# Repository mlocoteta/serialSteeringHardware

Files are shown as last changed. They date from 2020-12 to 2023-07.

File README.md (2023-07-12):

# LKAS/ECU Data Interceptor

This is open source hardware for use with 2016/2017 Honda Accord's with Nidec camera units. Other form factors aren't guaranteed to fit - use at your own risk!

Link which demonstrates functionality:
<https://youtu.be/dwGLrD5iYao>
# Boards
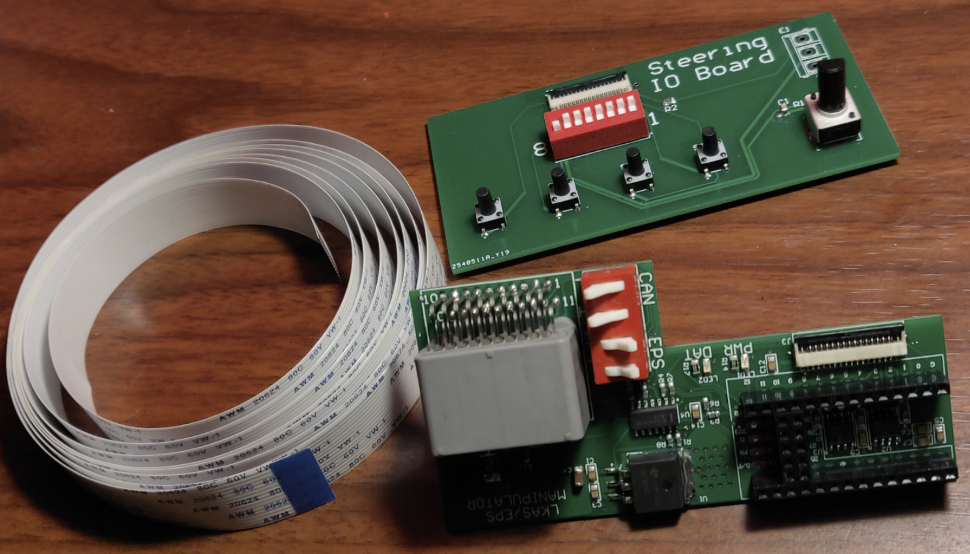
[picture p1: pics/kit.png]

There are two boards in this package:
1. The LKAS/ECU Manipulator
2. The debug board

To connect the debug board to the LKAS/ECU Manipulator a 15 position 0.1" ribbon cable should be used. This is needed for debugging and testing different scenarios.

## LKAS/ECU Manipulator V2

[Click here to purchase Development board.](https://devinstruments.com/)

Smaller form factor using STM32F1 MCU.

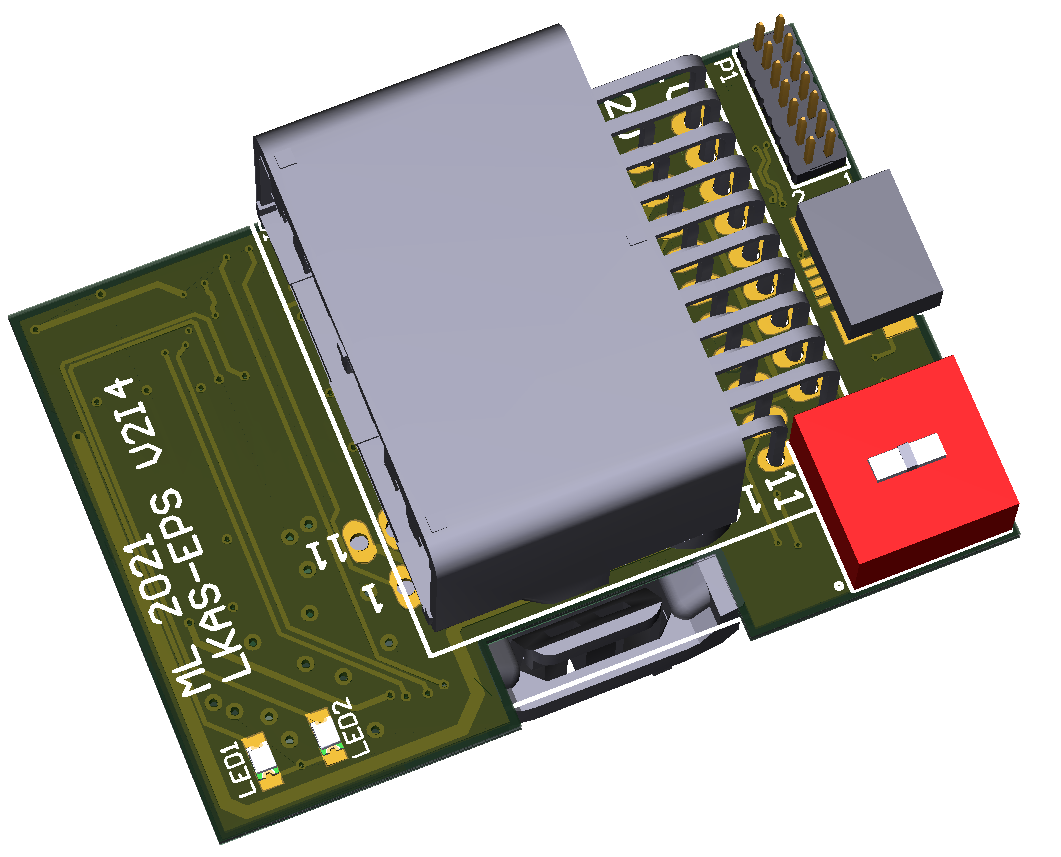
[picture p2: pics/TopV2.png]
LKAS/ECU Manipulator Version 2 (TOP)

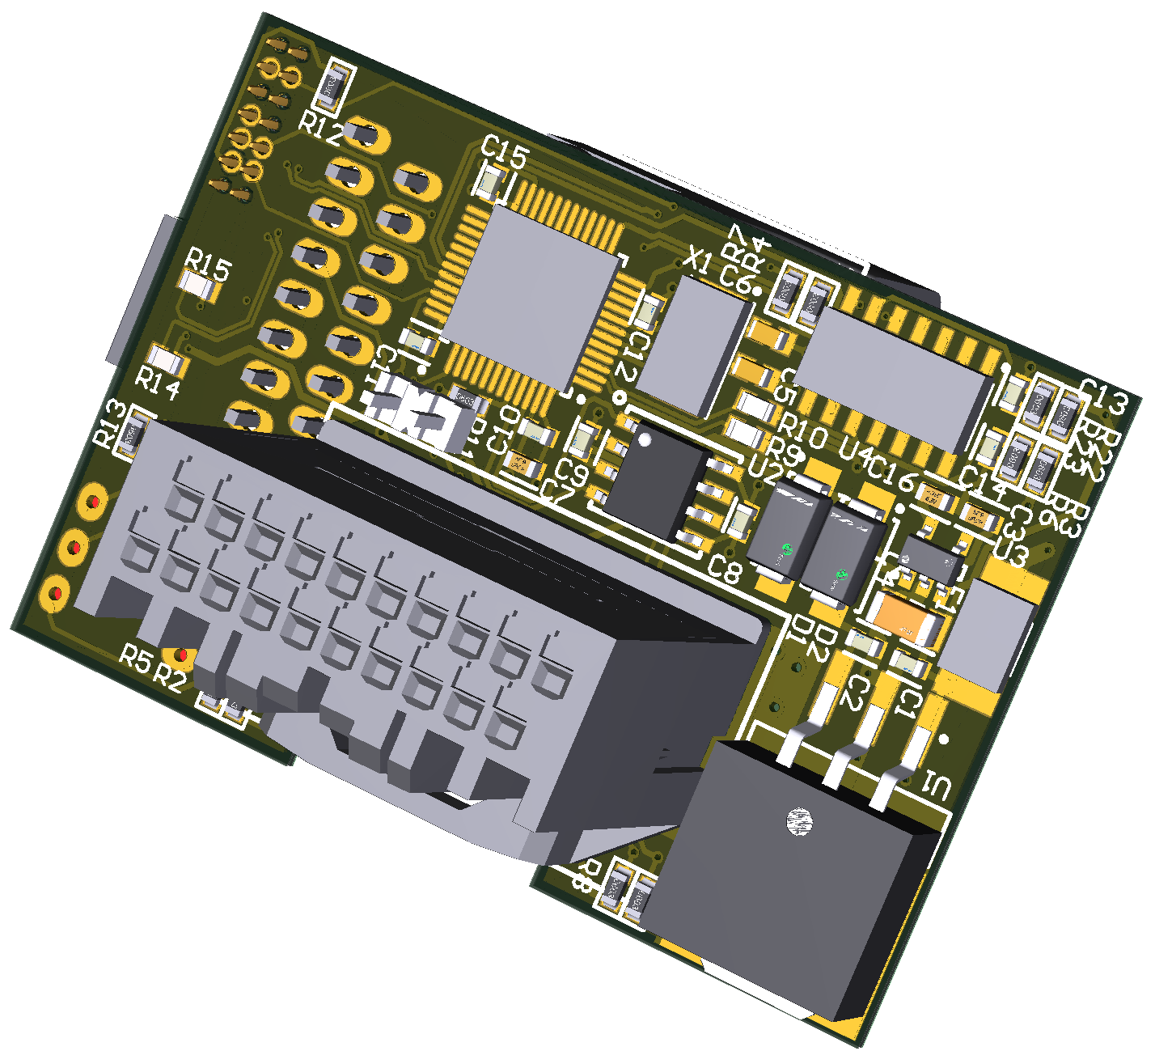
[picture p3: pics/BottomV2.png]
LKAS/ECU Manipulator Version 2 (Bottom)


## LKAS/ECU Manipulator V1

Below is the basic layout and functions of the board. 
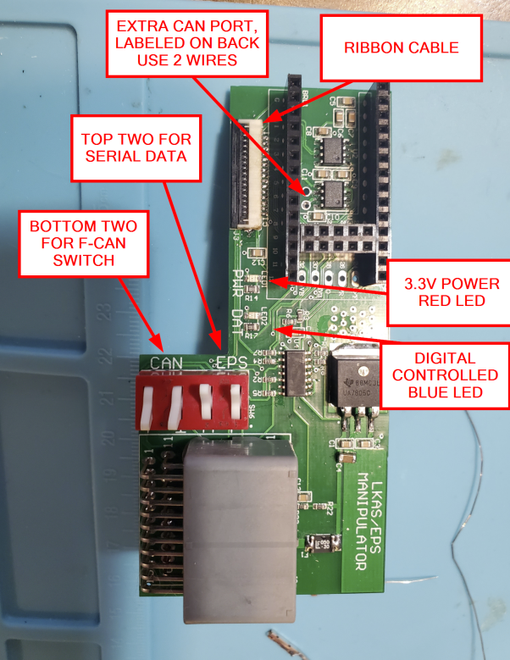
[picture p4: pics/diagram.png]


The board consists of: 
- A comparator for-
	- Level shifting the 12V to 3.3V to read serial information.
	- Level shifting the 3.3V UART to 12V to transmit on the vehicles serial line.
- Two MCP2562FDs for-
	- Transmitting/ receiving F-CAN from the vehicle
	- Transmitting/ receiving F-CAN to the camera unit.
		- **Note**: Typically this is not used.
- Debug Connector with GPIO and an ADC input
- Teensy 4.0 

When mounted the board is slightly larger than the the factory cover can contain. 
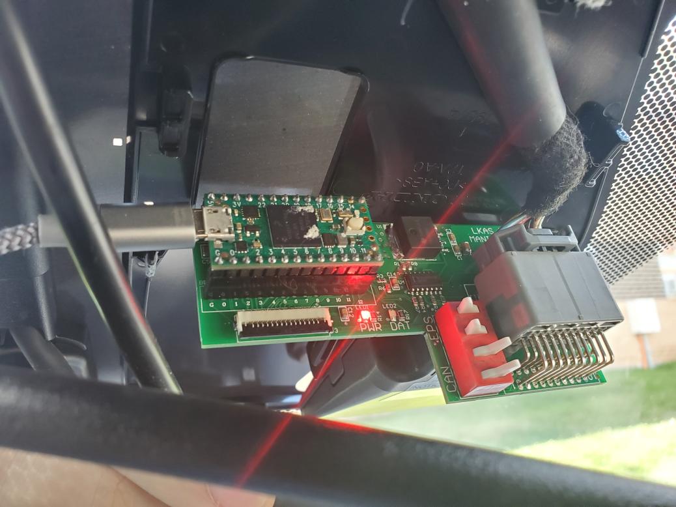
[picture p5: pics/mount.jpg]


## Debug Board
The board consists of: 
- A connection for a potentiometer **OR** a 3 block terminal for external resistance.
	- **Note**: This is current limited resulting in slightly lower/higher ADC readout values.
- 4 Tactile Push Buttons 
- 8 Position DIP Switch
	- *DIP 1-7* are digital IO
	- *DIP 8* to onboard POT/ External Pot
- Ribbon cable connector
## Firmware
For the latest OP open source firmware - visit:
V1 Board:
[https://github.com/reddn/AccordManualSteering](https://github.com/reddn/AccordManualSteering)

V2 Board:
[https://github.com/reddn/LINInterfaceV2](https://github.com/reddn/LINInterfaceV2)
In the Firmware Folder is an example sketch which simulates can simulate a brief torque to the steering wheel.

## License and Terms of Use:

Released under the MIT license.

**THIS IS ALPHA QUALITY HARDWARE AND IS INTENDED FOR OFF-ROAD USE AND RESEARCH PURPOSES ONLY.
YOU ARE RESPONSIBLE FOR COMPLYING WITH LOCAL LAWS AND REGULATIONS.
NO WARRANTY EXPRESSED OR IMPLIED.**

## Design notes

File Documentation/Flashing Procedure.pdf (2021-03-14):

Flashing Procedure | 03/14/2021

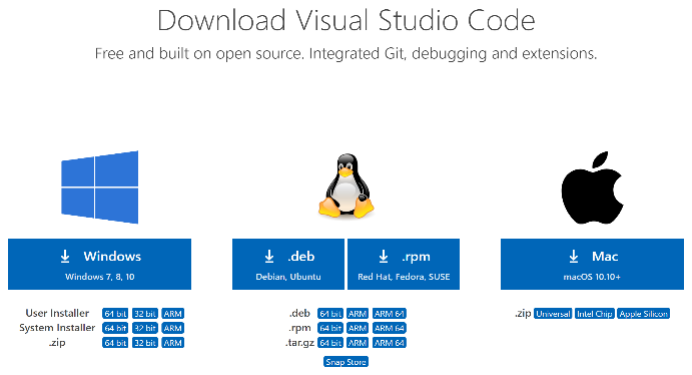
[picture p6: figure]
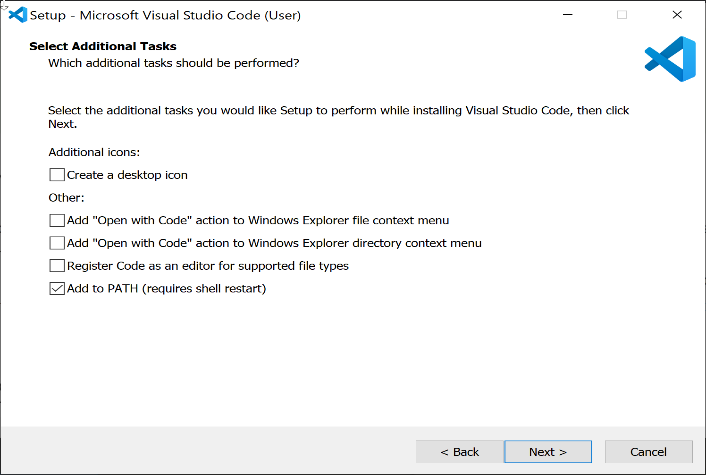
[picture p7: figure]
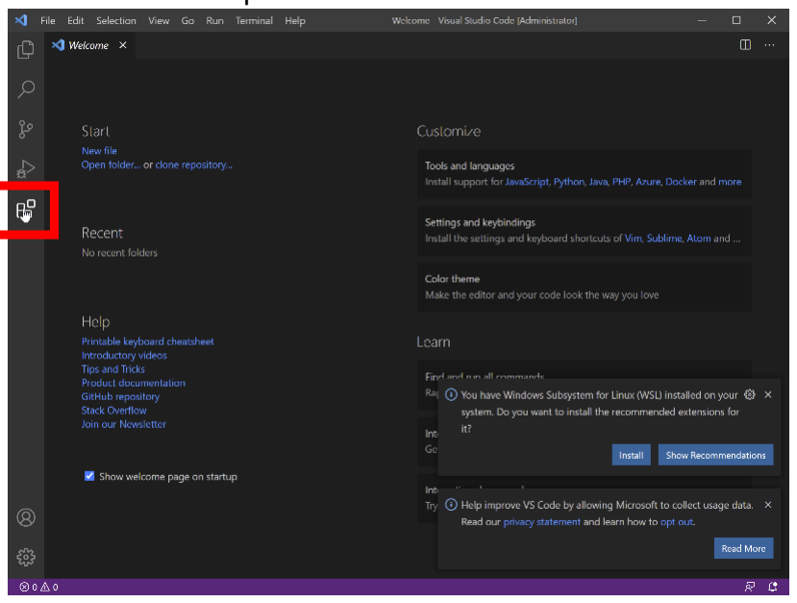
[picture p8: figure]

Doc Rev: A | Page 1 of 6

The EPS-LKAS V2 board is equipped with a Micro-B USB for flashing. The scope of this document is to get your computer setup with the necessary software to update and modify the firmware on your (Windows) computer.

1. Download and install Visual Studio Code. https://code.visualstudio.com/download
a. Download the program selecting the appropriate OS. Windows 10 will be used as an example for this document.
b. The default options should be fine for normal use, however, check options as needed.
c. Launch VS Code.
2. Download Platform IO.
a. Select the “Extensions Option”

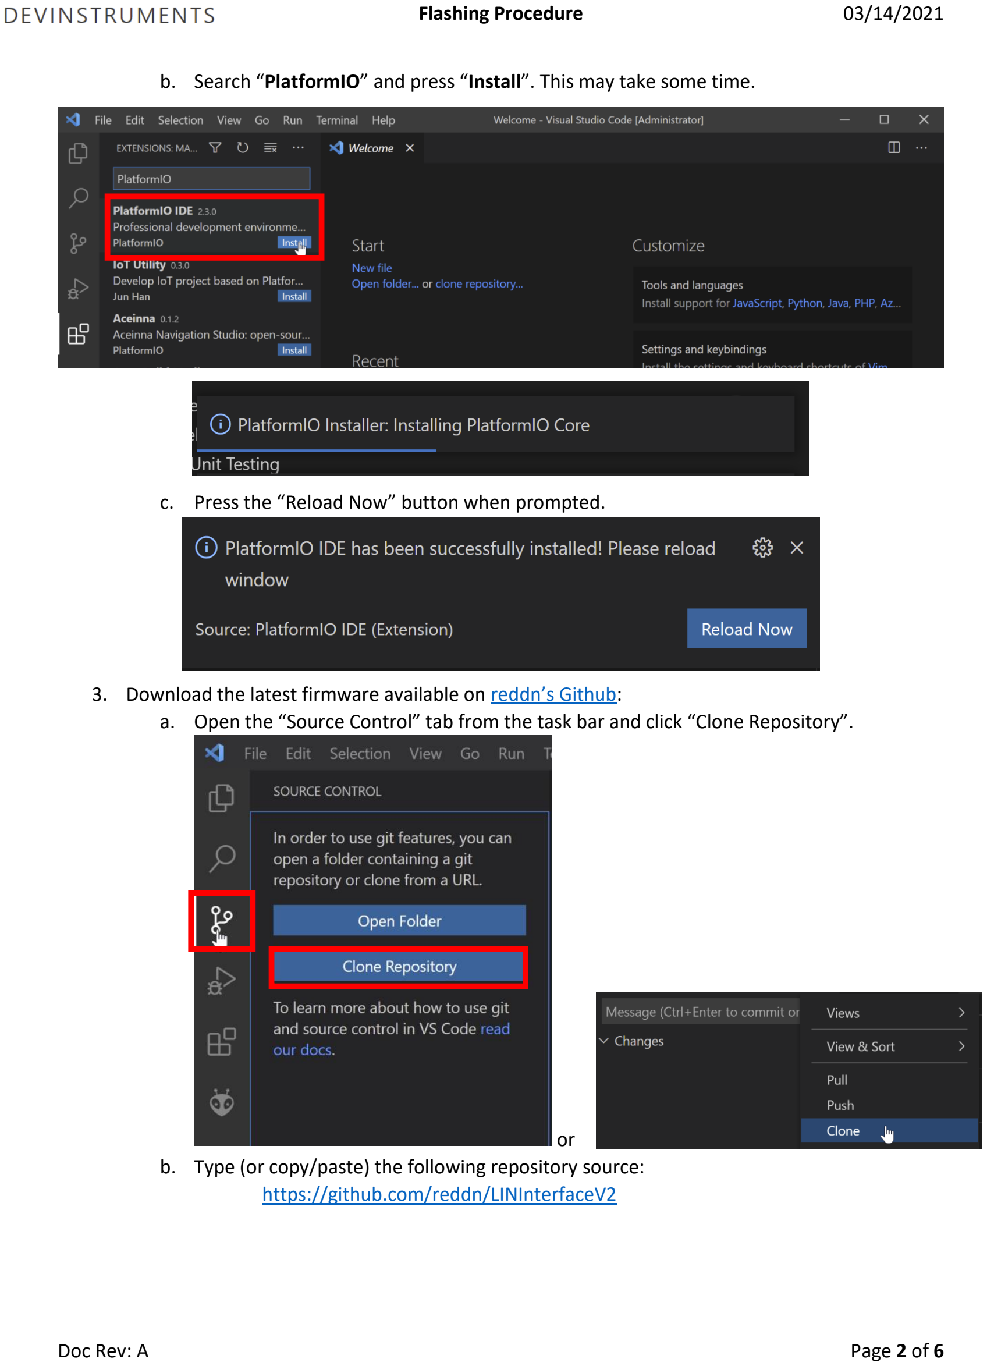
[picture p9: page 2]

b. Search “PlatformIO” and press “Install”. This may take some time.
c. Press the “Reload Now” button when prompted.
3. Download the latest firmware available on reddn’s Github: (https://github.com/reddn/LINInterfaceV2)
a. Open the “Source Control” tab from the task bar and click “Clone Repository”.

or
b. Type (or copy/paste) the following repository source: https://github.com/reddn/LINInterfaceV2

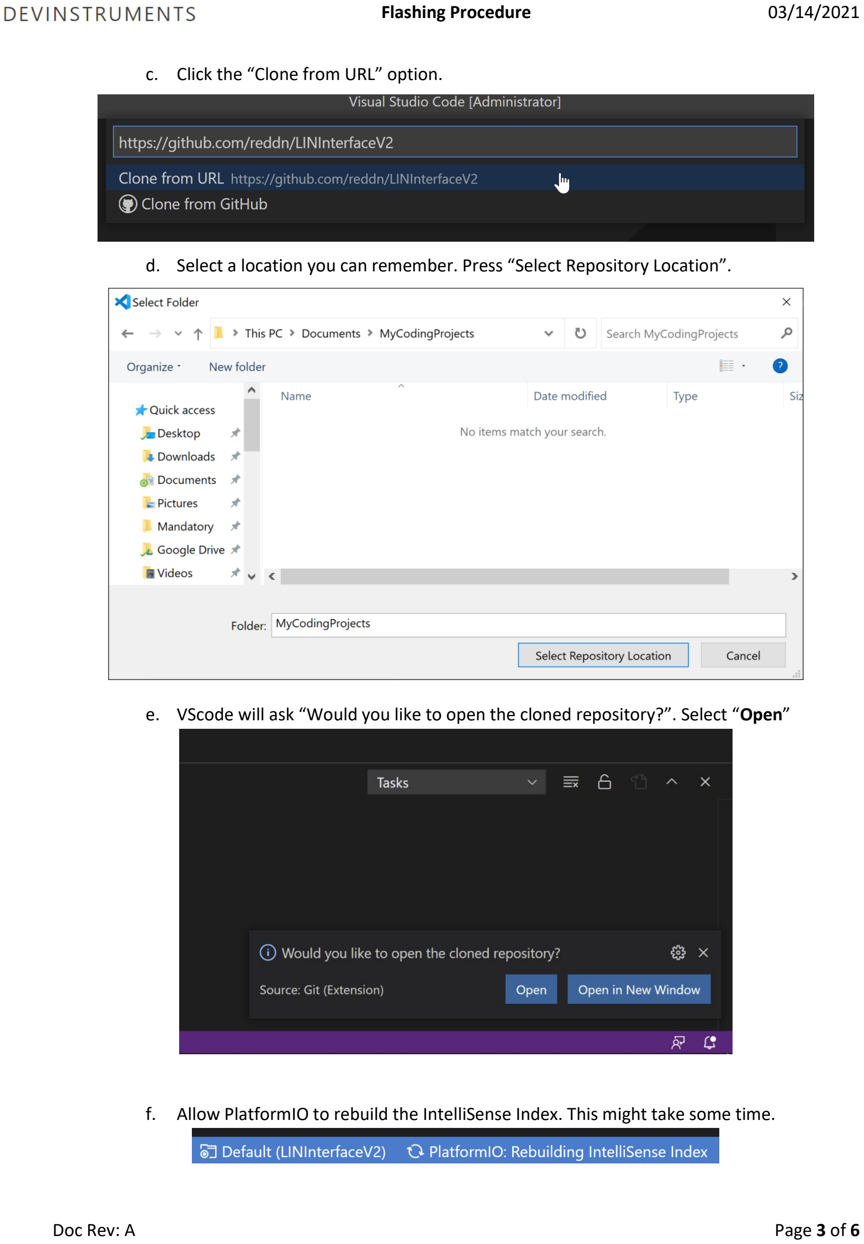
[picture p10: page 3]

c. Click the “Clone from URL” option.
d. Select a location you can remember. Press “Select Repository Location”.
e. VScode will ask “Would you like to open the cloned repository?”. Select “Open”
f. Allow PlatformIO to rebuild the IntelliSense Index. This might take some time.

4. The STM32duino USB drivers must be installed. Download the files from rogerclarkmelbourne’s github. (https://github.com/rogerclarkmelbourne/Arduino_STM32/tree/master/drivers)
a. Download the entire repo here using the link below: https://github.com/rogerclarkmelbourne/Arduino_STM32/archive/master.zip
i. Alternatively, use a website to download the drivers only.
1. i.e. Use “gitzip” (http://kinolien.github.io/gitzip/) and paste the linkw: https://github.com/rogerclarkmelbourne/Arduino_STM32/tree/master/drivers
b. Unzip the file and navigate to the drivers/win/ folder.
c. Run “install_drivers.bat” as administrator.

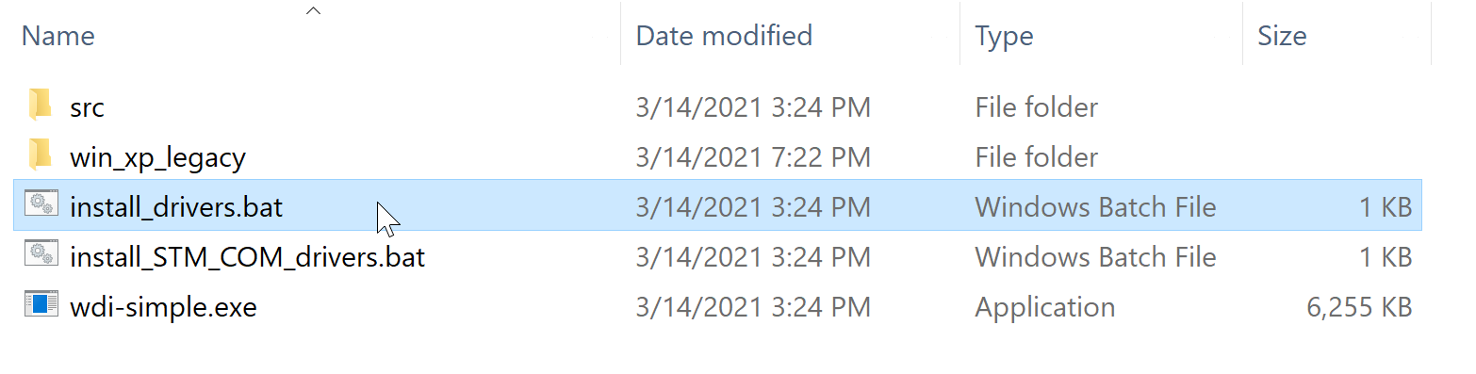
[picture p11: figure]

d. Allow the command line to install the drivers and once done “Press any key to continue …” message appears.
5. Flashing the board.

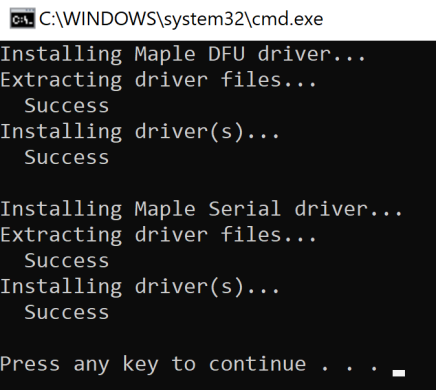
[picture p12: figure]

a. Plug the Micro-B USB able into the circuit board.
i. Do NOT plug the other end of the cable into the computer yet.

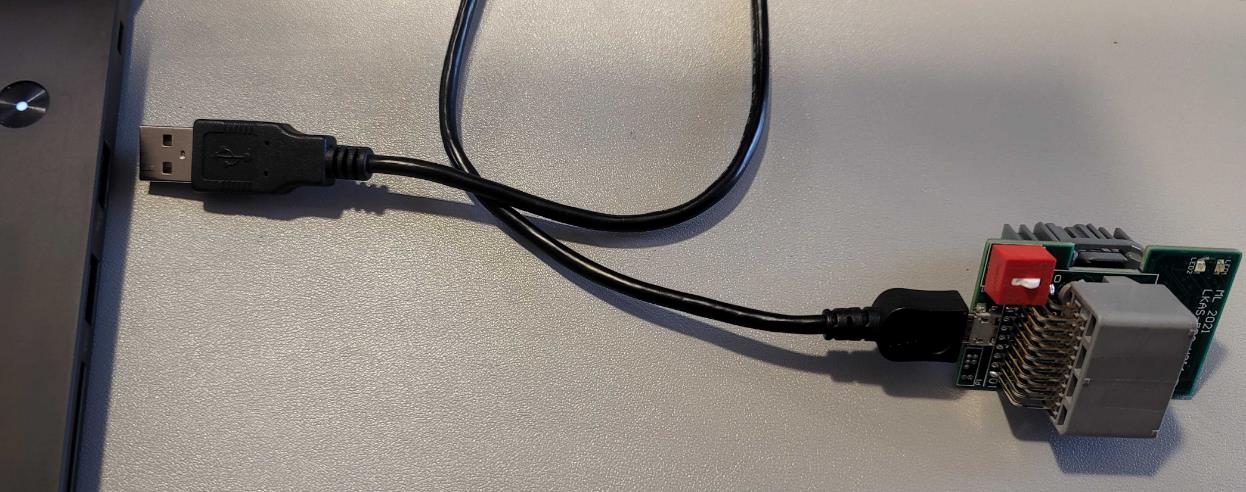
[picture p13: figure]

b. Have the source code open and press the “Upload” to build and upload the code.

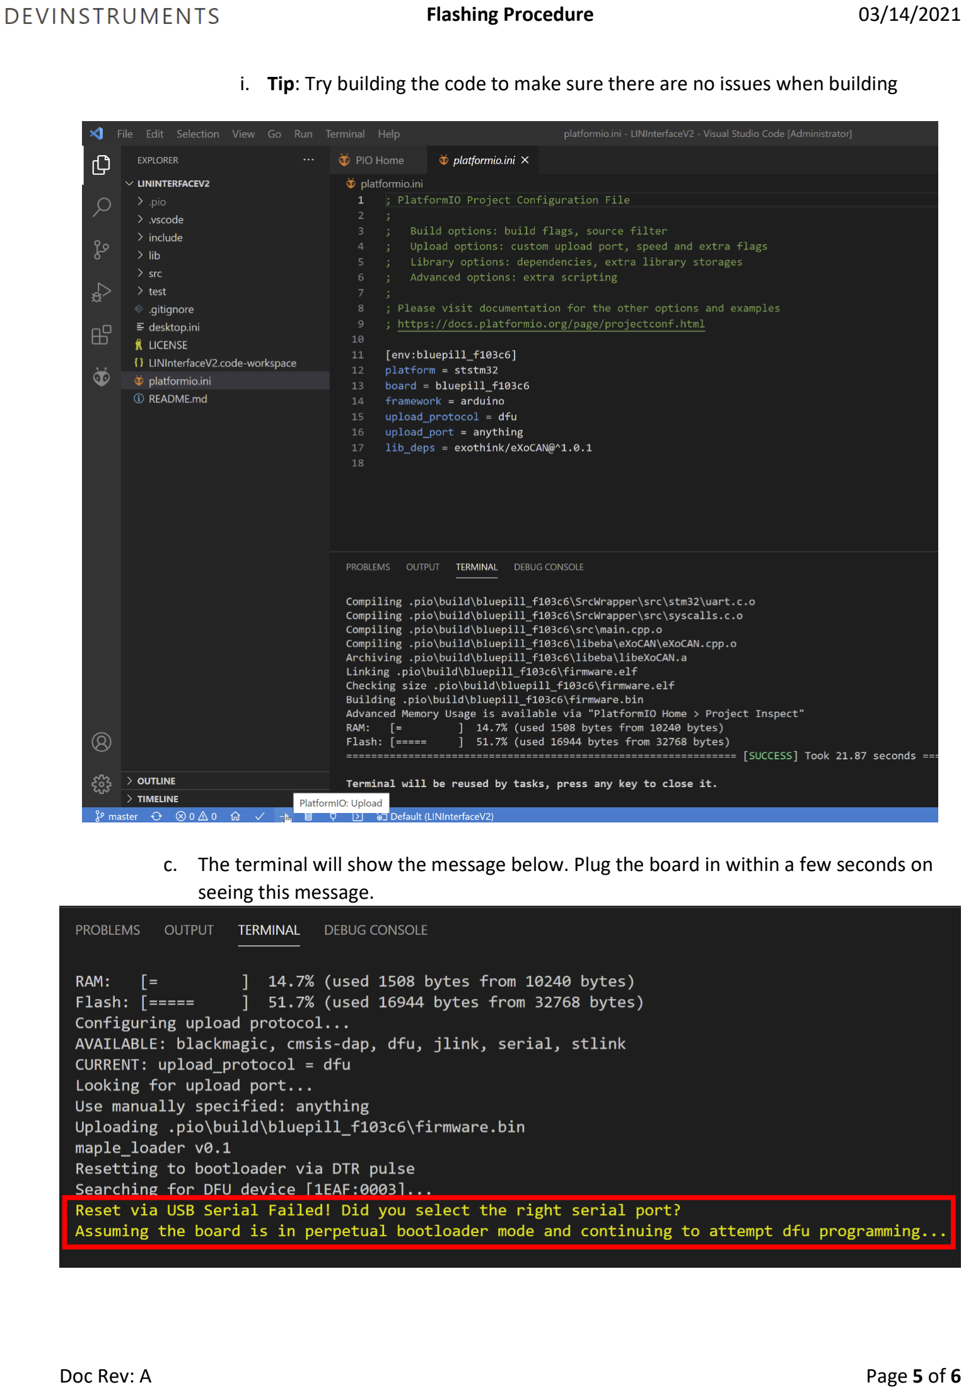
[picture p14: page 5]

i. Tip: Try building the code to make sure there are no issues when building
c. The terminal will show the message below. Plug the board in within a few seconds on seeing this message.

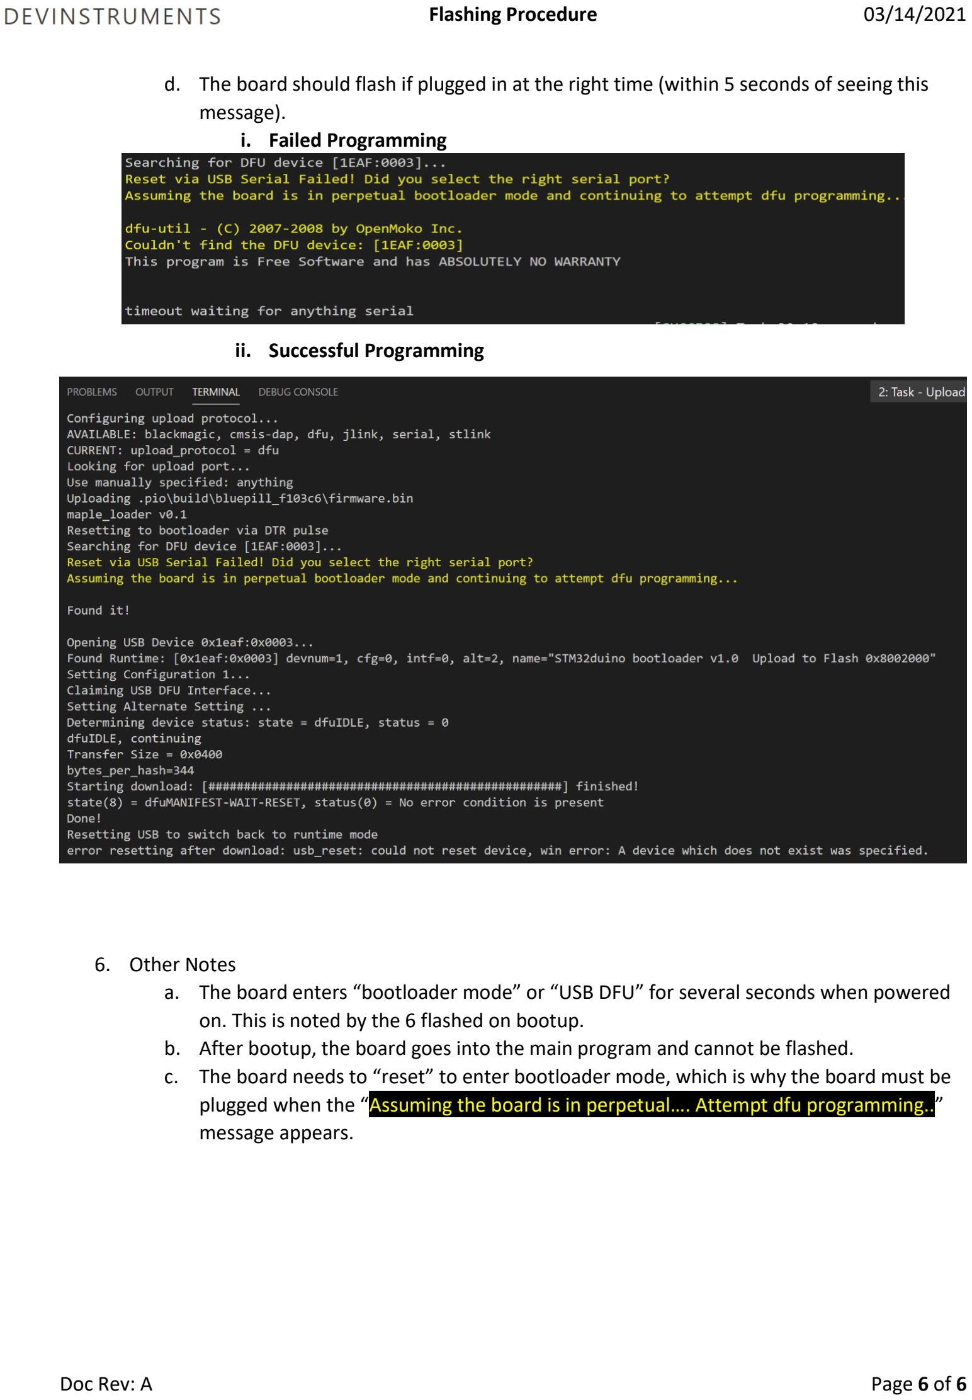
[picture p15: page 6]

d. The board should flash if plugged in at the right time (within 5 seconds of seeing this message).
i. Failed Programming

ii. Successful Programming

6. Other Notes
a. The board enters “bootloader mode” or “USB DFU” for several seconds when powered on. This is noted by the 6 flashed on bootup.
b. After bootup, the board goes into the main program and cannot be flashed.
c. The board needs to “reset” to enter bootloader mode, which is why the board must be plugged when the “Assuming the board is in perpetual…. Attempt dfu programming..” message appears.

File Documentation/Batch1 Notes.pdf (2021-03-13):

Batch 1 Notes | 03/07/2021

Each board is hand assembled, all solder joints are checked via microscope and tested on the road for at least an hour- so you can rest assured the hardware is in working condition. There are some things we should note about the Batch 1 boards, so I would like to highlight the details in this document.

1. SPDT DIP SWITCH: Controls if the serial steering lines are bypassed or not.
a. Flipped towards the passenger (flat side towards C2) allowed the board to manipulate the EPStoLKAS and LKAStoEPS line.
b. Flipped towards the driver (flat side towards C1) is bypassed and the board does not manipulate the signals.
2. USB Micro B Connector: Used to update board firmware.
a. Note: The board can only be programmed when either vehicle power is off OR when not connected to the vehicle.
b. Refer to programming guide (coming soon).
3. SWD Header: Used to program bootloader.
a. STLINK-V3MINI and GRPB072VWVN-RC header required.
4. BLUE LED: Used as a heartbeat to validate the board is receiving power, CAN and makes it through the main loop.
a. When first booted, there will be 6 flashes. This is “bootloader mode” and allows the board to be programmed.
b. After the first 6 flashes, the board should enter the main program and have a 250ms heartbeat (at the time of this writing.
5. FAULT (RED) LED: Used to indicate fault based on various conditions in the code. The fault is viewable on CAN, via message 0x18F (STEER_STATUS).
a. This can only be reset by restarting the vehicle and will not allow OP to engage.
6. Locking Tab: Allows (relatively) easy removal from the multipurpose camera unit (MCU).

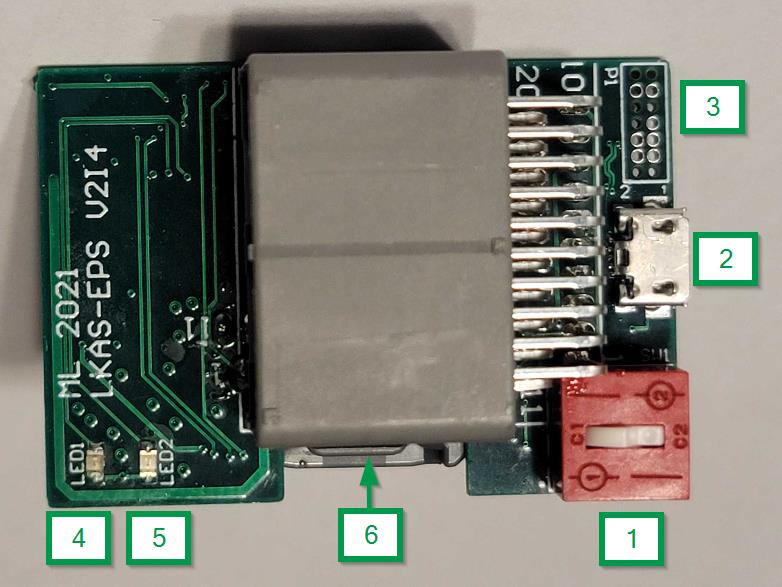
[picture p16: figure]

Batch 1 Notes | 03/07/2021
7. Flux Residue: As you can probably tell, the board is hand soldered. And with hand soldering comes no-clean flux! So, the flux residue on the board isn’t a concern, while it may not be visually ideal.
8. Bodge #1: It was noticed that a pullup resistor was needed on the USB D+ line after PCB fabrication, therefore the resistor and wire were added after the fact. Handle with care to avoid damage!
9. Solder “Glob”: It was noticed that the internal pulldown of BOOT1 was not strong enough in cold temperatures which would result in erratic bootup. Therefore, the pin has been manually shorted to ground to resolve this issue. This solder joint is not a cause for concern.
10. B-CAN (pin 6 and pin 17): While not noted on the schematic, the B-CAN lines were added post process and should pass through without any problems.

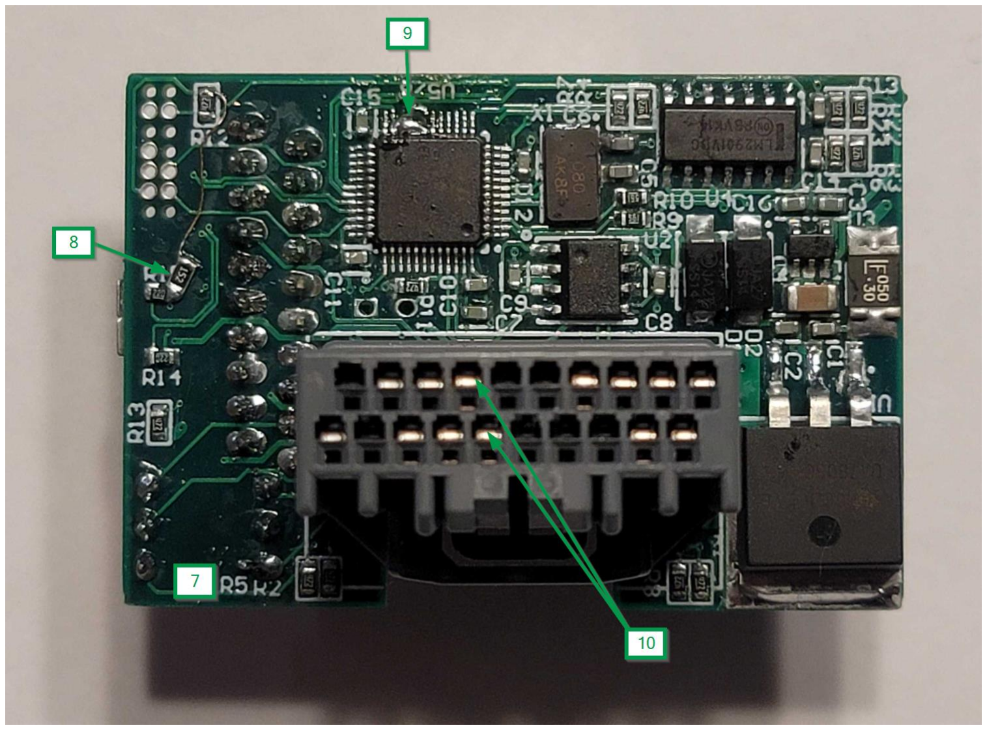
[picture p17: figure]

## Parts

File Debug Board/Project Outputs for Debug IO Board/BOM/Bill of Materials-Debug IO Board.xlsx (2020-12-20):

Comment | Description | Designator | Footprint | LibRef | Quantity
C0805C105K4PACTU |  | C1 | CAPC2013X145X50LL20T25 | CMP-2007-01016-1 | 1
1760500000 | OMNIMATE Signal - series PM | E1 | PM_5_08_90_03 | CMP-1559-01629-1 | 1
686115148922 | SMT ZIF Connectors Hinge Type WR-FPC, Horizontal, Bottom Contact, pitch 1 mm, 15 pins | J1 | 686115148922 | CMP-1502-01518-1 | 1
PTV09A-4020U-B103 | POT 10K OHM 1/20W CARBON LINEAR | R1 | FP-PTV09A-4-MFG | CMP-07234-000013-1 | 1
RC0805FR-071KL | Chip Resistor, 1 KOhm, +/- 1%, 125 mW, -55 to 155 degC, 0805 (2012 Metric), RoHS, Tape and Reel | R2 | RESC2013X60X35ML10T20 | CMP-2100-03671-1 | 1
1825910-6 | Tact Switch, SPST-NO, 0.05 A, -35 to 85 degC, 4-Pin THD, RoHS, Bulk | SW1, SW2, SW3, SW4 | TECO-1825910-6_V | CMP-1684-00021-1 | 4
78B08ST | SWITCH SLIDE DIP SPST 150MA 30V | SW5 | FP-78B08ST-MFG | CMP-31942-000004-1 | 1

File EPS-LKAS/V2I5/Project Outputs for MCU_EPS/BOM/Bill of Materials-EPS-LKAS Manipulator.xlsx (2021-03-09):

Comment | Description | Designator | Footprint | LibRef | Quantity
C0603C104M3RACTU | CAP CER 0.1UF 25V X7R 0603 | C1, C2, C8, C9, C10, C11, C12, C13, C14, C15 | FP-C0603C-CF-MFG | CMP-2006-03065-2 | 10
CL10B475KQ8NQNC | CAP CER 4.7UF 6.3V X7R 0603 | C3, C7, C16 | FP-CL10-IPC_C | CMP-2000-06096-2 | 3
CL31A106KBHNNNE | CAP CER 10UF 50V X5R 1206 | C4 | FP-CL31-IPC_C | CMP-13271-000016-1 | 1
GRM1885C1H220JA01D | Chip Capacitor, 22 pF, +/- 5%, 50 V, -55 to 125 degC, 0603 (1608 Metric), RoHS, Tape and Reel | C5, C6 | CAPC1608X90X35ML10T15 | CMP-2000-04945-1 | 2
SS14 | DIODE SCHOTTKY 40V 1A SMA | D1, D2 | FP-403AE-MFG | CMP-2000-04943-2 | 2
1812L050/30PR | PTC Resettable Fuse, 0.8 W, 30 V, -40 to 85 degC, 2-Pin SMD, RoHS, Tape and Reel | F1 | LFUS-1812L05030PR_V | CMP-2000-05508-1 | 1
MX34020SF1 | Automotive Connectors Sckt HOUSING 20P | J1 | MX34020SF1 | MX34020SF1 | 1 | Note, pins are needed - no PCB equivalent exists.
MX34020NF1 | JAE MX34 Series, 2.2mm Pitch 20 Way 2 Row Right Angle PCB Header, Solder Termination, 3A | J2 | MX34020NF1 | MX34020NF1 | 1
10118192-0001LF | Micro USB B Type Receptacle, -55 to 85 degC, 5-Pin SMD, RoHS, Tape and Reel | J3 | FCI-10118192-0001LF-5_V | CMP-2000-05118-1 | 1
150080SS75000 | SMD mono-color Chip LED, WL-SMCW, Super Red | LED1 | 0805_A | CMP-1426-00010-1 | 1
150080BS75000 | SMD mono-color Chip LED, WL-SMCW, Blue | LED2 | 0805_A | CMP-1426-00008-1 | 1
4K7 | Res Thick Film 0603 4.7K Ohm 1% 1/10W 100ppm/C Molded SMD SMD Paper T/R | R1, R2, R3, R4, R5, R6, R7, R8, R11, R12, R13, R22, R23, R17 | R0603 | RMCF0603FT4K70 | 13
RC0603FR-07560RL | Chip Resistor, 560 Ohm, +/- 1%, 0.1 W, -55 to 155 degC, 0603 (1608 Metric), RoHS, Tape and Reel | R9, R10 | RESC1608X55X25ML10T15 | CMP-1659-00038-1 | 2
CRCW060322R0JNTA | 22R 0603 | R14, R15 | RESC1609X50X30ML10T20 | CMP-2000-03099-1 | 2
76STC02T | SWITCH TOGGLE DIP SPDT 150MA 30V WIRED: 1 2 3 4 5 6 | SW1 | 76STC02T | 76STC02T | 1
UA7805CKTTR | Fixed Positive Voltage Regulator, 7 to 25 V, 1.5 A, 0 to 125 degC, 3-Pin DDPAK (KTT), Green (RoHS & no Sb/Br), Tape and Reel | U1 | KTT0003A_V | CMP-1685-00014-1 | 1
MCP2562FD-E/SN | 8 SOIC 3.90mm(.150in) TUBECAN Flexible Data Rate Transceiver | U2 | MCP2561 | MCP2562FD-E/SN | 1
MIC5504-3.3YM5-TR | IC REG LINEAR 3.3V 300MA SOT23-5 | U3 | FP-SOT23-5LD-PL-1-MFG | CMP-2000-07604-2 | 1
NCV2901DR2G | Comparator General Purpose CMOS, Open-Collector, TTL 14-SOIC | U4 | ONSC-SOIC-14-751A-03_V | CMP-1305-00036-1 | 1
STM32F103C6T7ATR | ARM Cortex-M3 32-bit MCU, 32 KB Flash, 10 KB Internal RAM, 37 I/Os, 48-pin LQFP, -40 to 105 degC, Tape and Reel | U5 | STM-LQFP48_L | CMP-0237-00257-3 | 1 or u6 | Select U5 or equivalent for LQFP48 footprint
STM32F103C6U6A | ARM Cortex-M3 32-bit MCU, 32 KB Flash, 10 KB Internal RAM, 37 I/Os, 48-pin UFQFPN, -40 to 85 degC, Tray | U6 | STM-UFQFPN48_M | CMP-0237-00046-3 | 1 or U5 | Select U6 or quivalent for UFQFPN48 footprint
ABM7-8.000MHZ-D2Y-T | Microprocessor Crystal, 8 MHz, 18 PF, -40 to 85 degC, 2-Pin SMD, RoHS, Tape and Reel | X1 | ABRA-ABM7-2_V | CMP-2000-05034-1 | 1
B3S-1000 | SWITCH SMT | SW2 |  |  | 1

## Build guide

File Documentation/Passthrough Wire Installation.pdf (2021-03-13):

Passthrough Wire Installation | 03/12/2021

The Comma Nidec harness does not come with the required LKAStoEPS and EPStoLKAS passthrough wires installed. Without these wires, the LKAS/EPS board cannot function.

To solve this problem, jumper wires are supplied with the board and must be installed.

1. Unlock each the retaining clip on the MX34 connectors. A screwdriver and some force may be required. The clip should release approximately 0.5 mm.

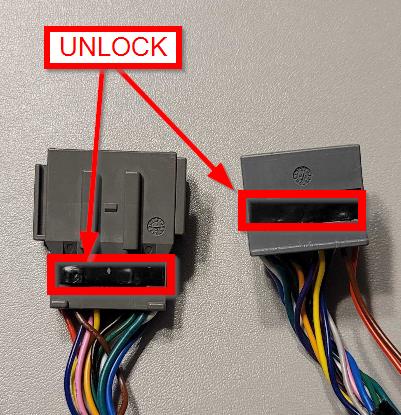
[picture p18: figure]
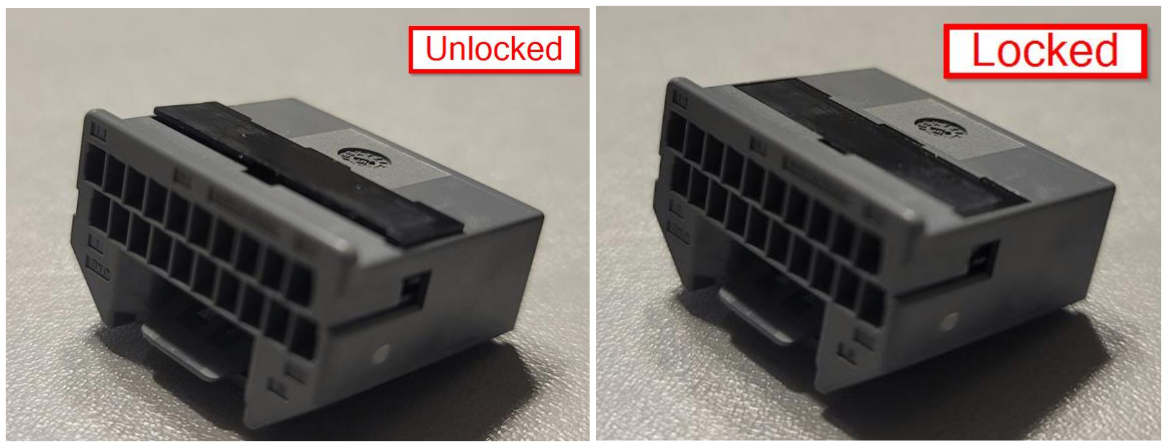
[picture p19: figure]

2. Locate Pin 1 and Pin 12 on each connector. The wires must be connected from 1A to 1B and from 12A to 12B.

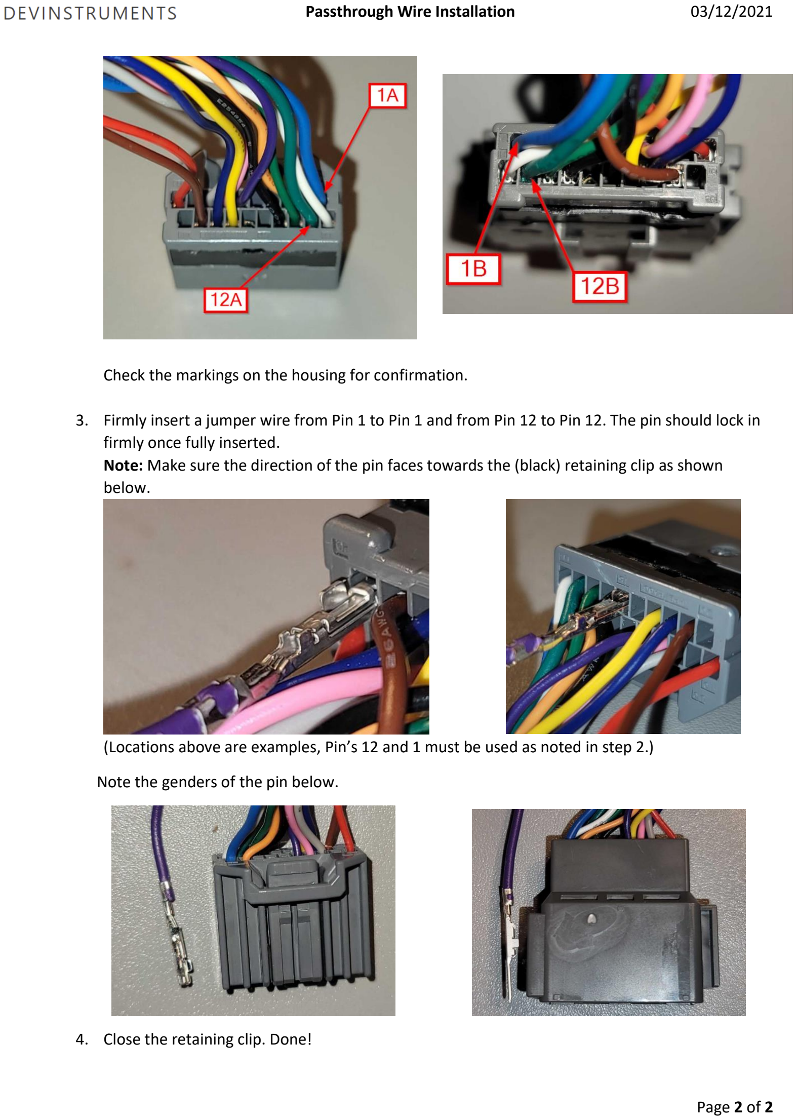
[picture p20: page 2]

Passthrough Wire Installation | 03/12/2021

Check the markings on the housing for confirmation.

3. Firmly insert a jumper wire from Pin 1 to Pin 1 and from Pin 12 to Pin 12. The pin should lock in firmly once fully inserted.
Note: Make sure the direction of the pin faces towards the (black) retaining clip as shown below.

(Locations above are examples, Pin’s 12 and 1 must be used as noted in step 2.)

Note the genders of the pin below.

4. Close the retaining clip. Done!

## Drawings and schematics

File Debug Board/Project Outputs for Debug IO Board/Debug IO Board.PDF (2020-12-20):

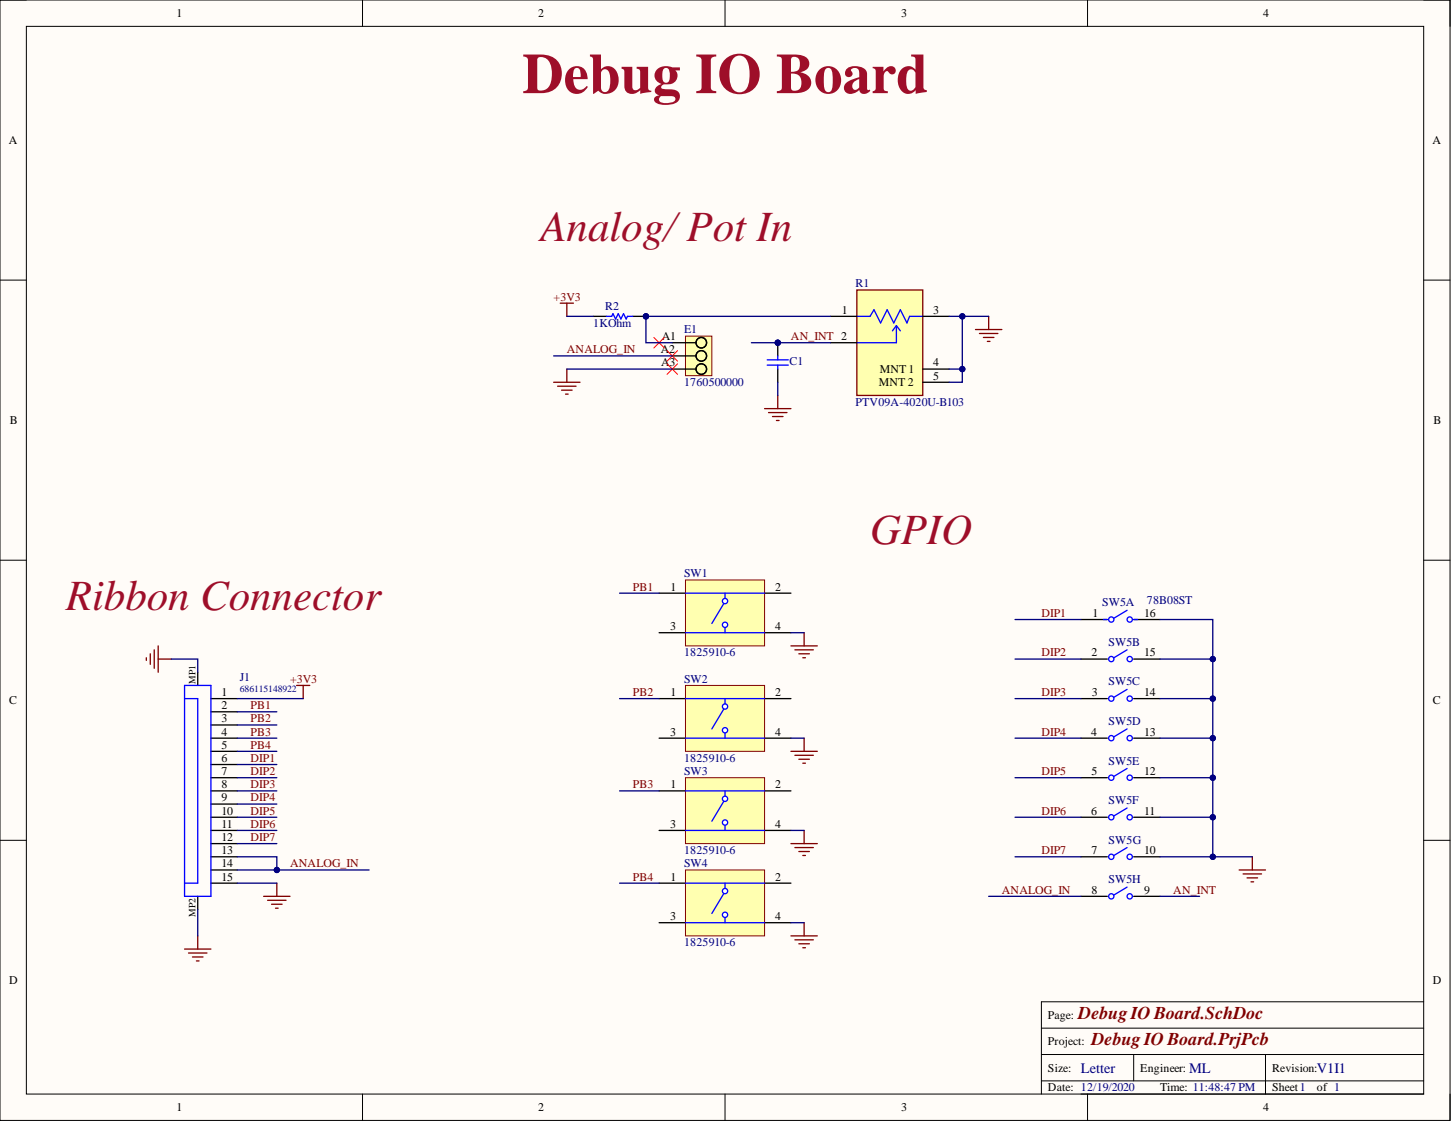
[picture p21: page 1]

Debug IO Board.SchDoc
Page:
Project: Debug IO Board.PrjPcb

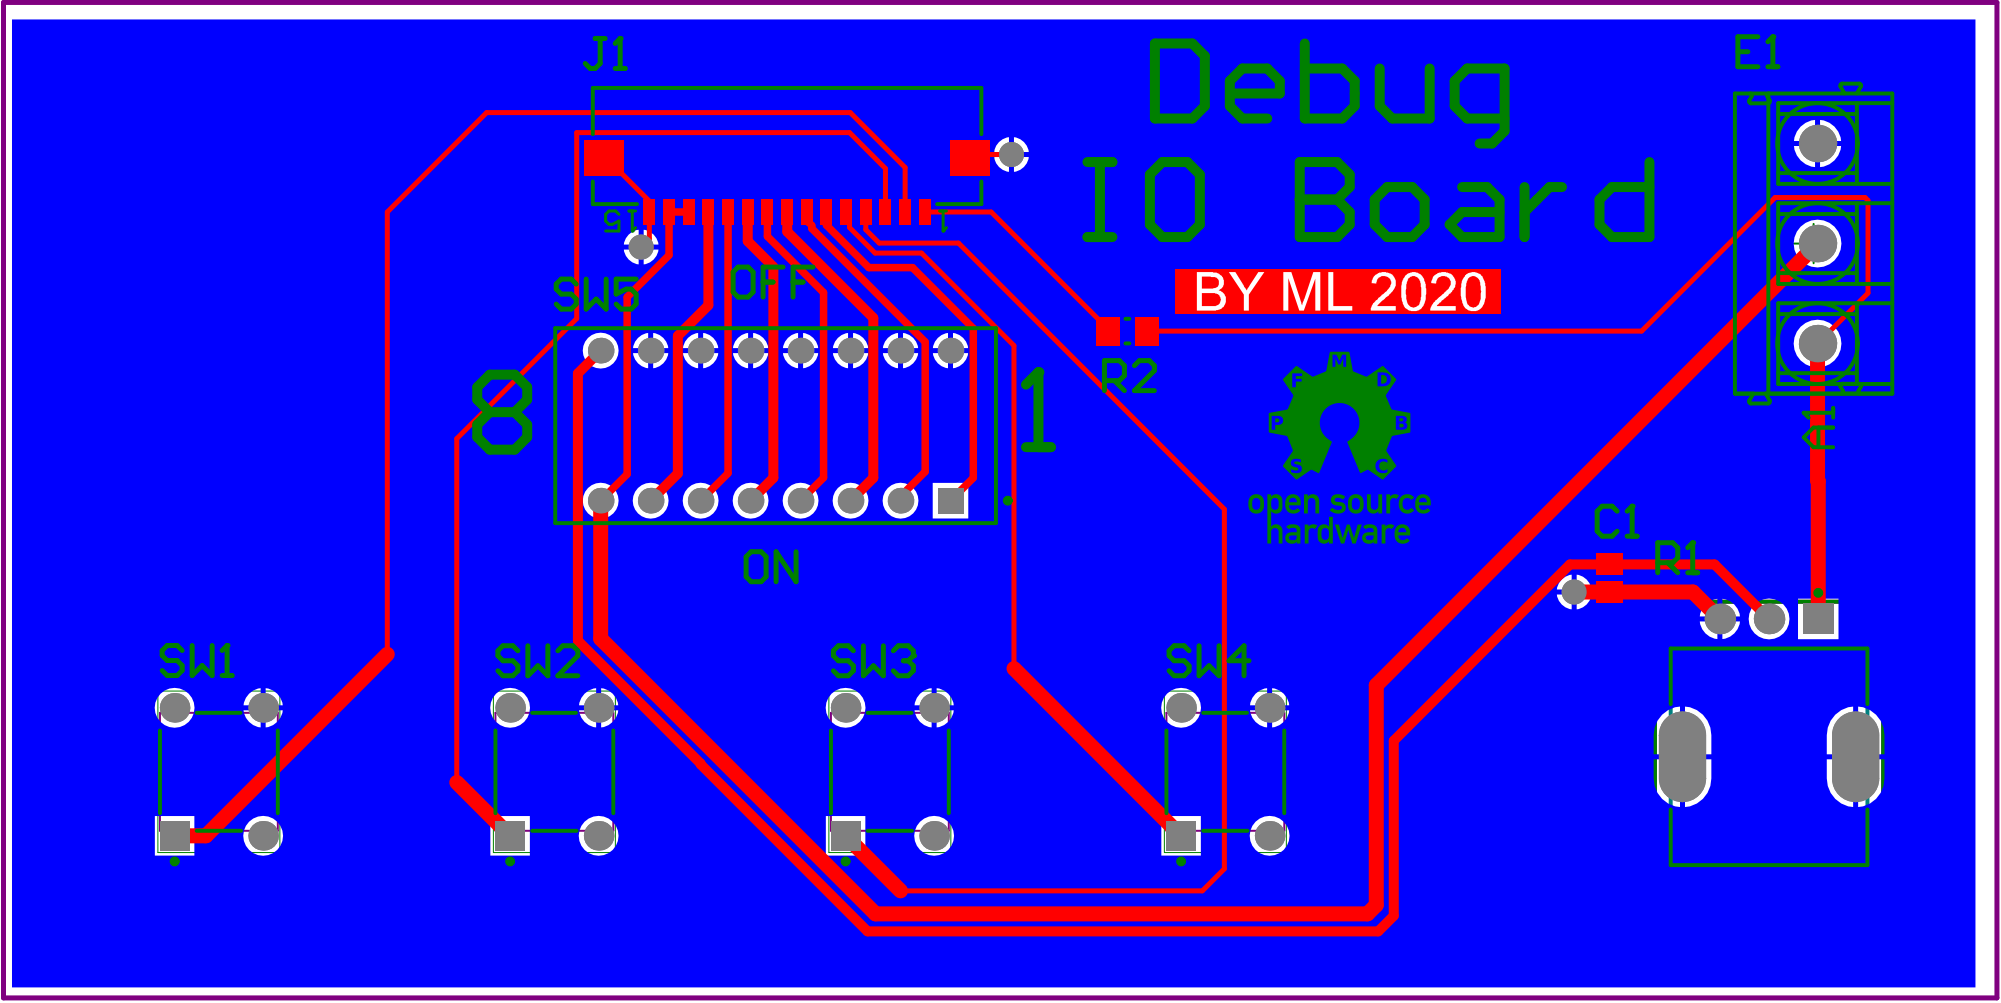
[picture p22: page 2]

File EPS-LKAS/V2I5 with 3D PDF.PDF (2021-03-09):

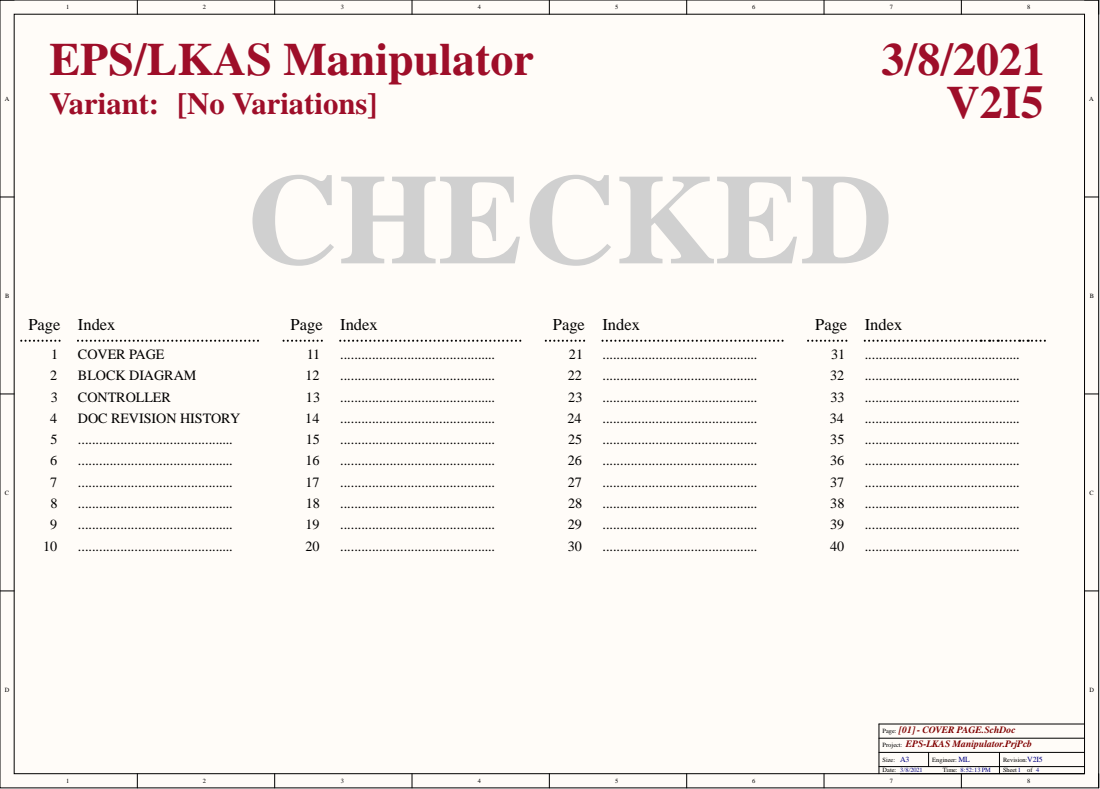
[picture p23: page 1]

[01] - COVER PAGE.SchDoc
Page:
Project: EPS-LKAS Manipulator.PrjPcb

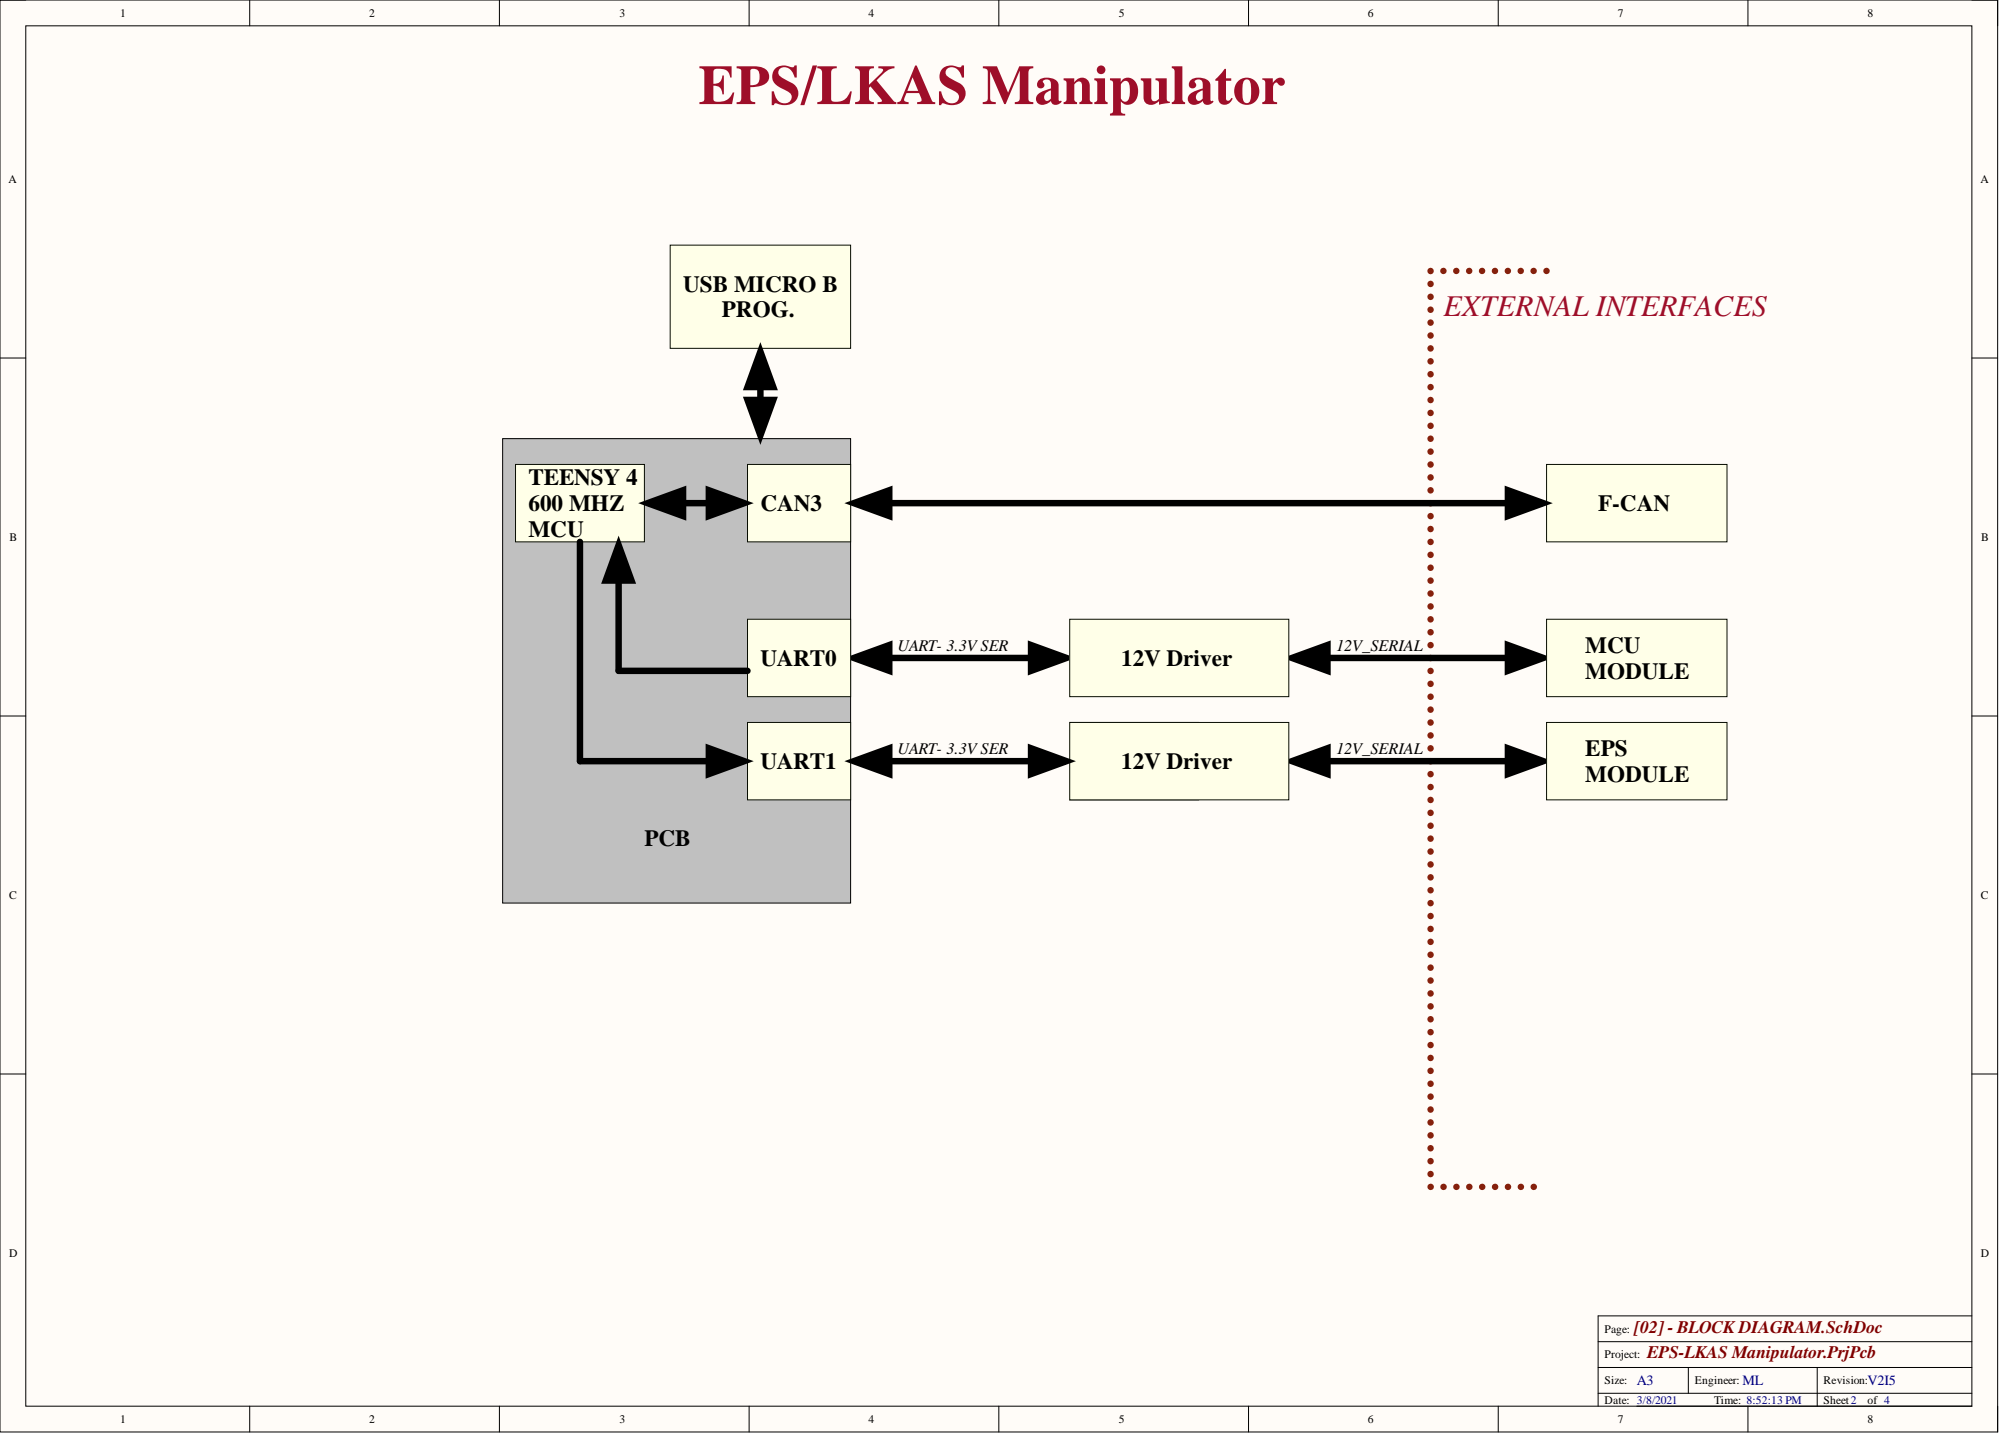
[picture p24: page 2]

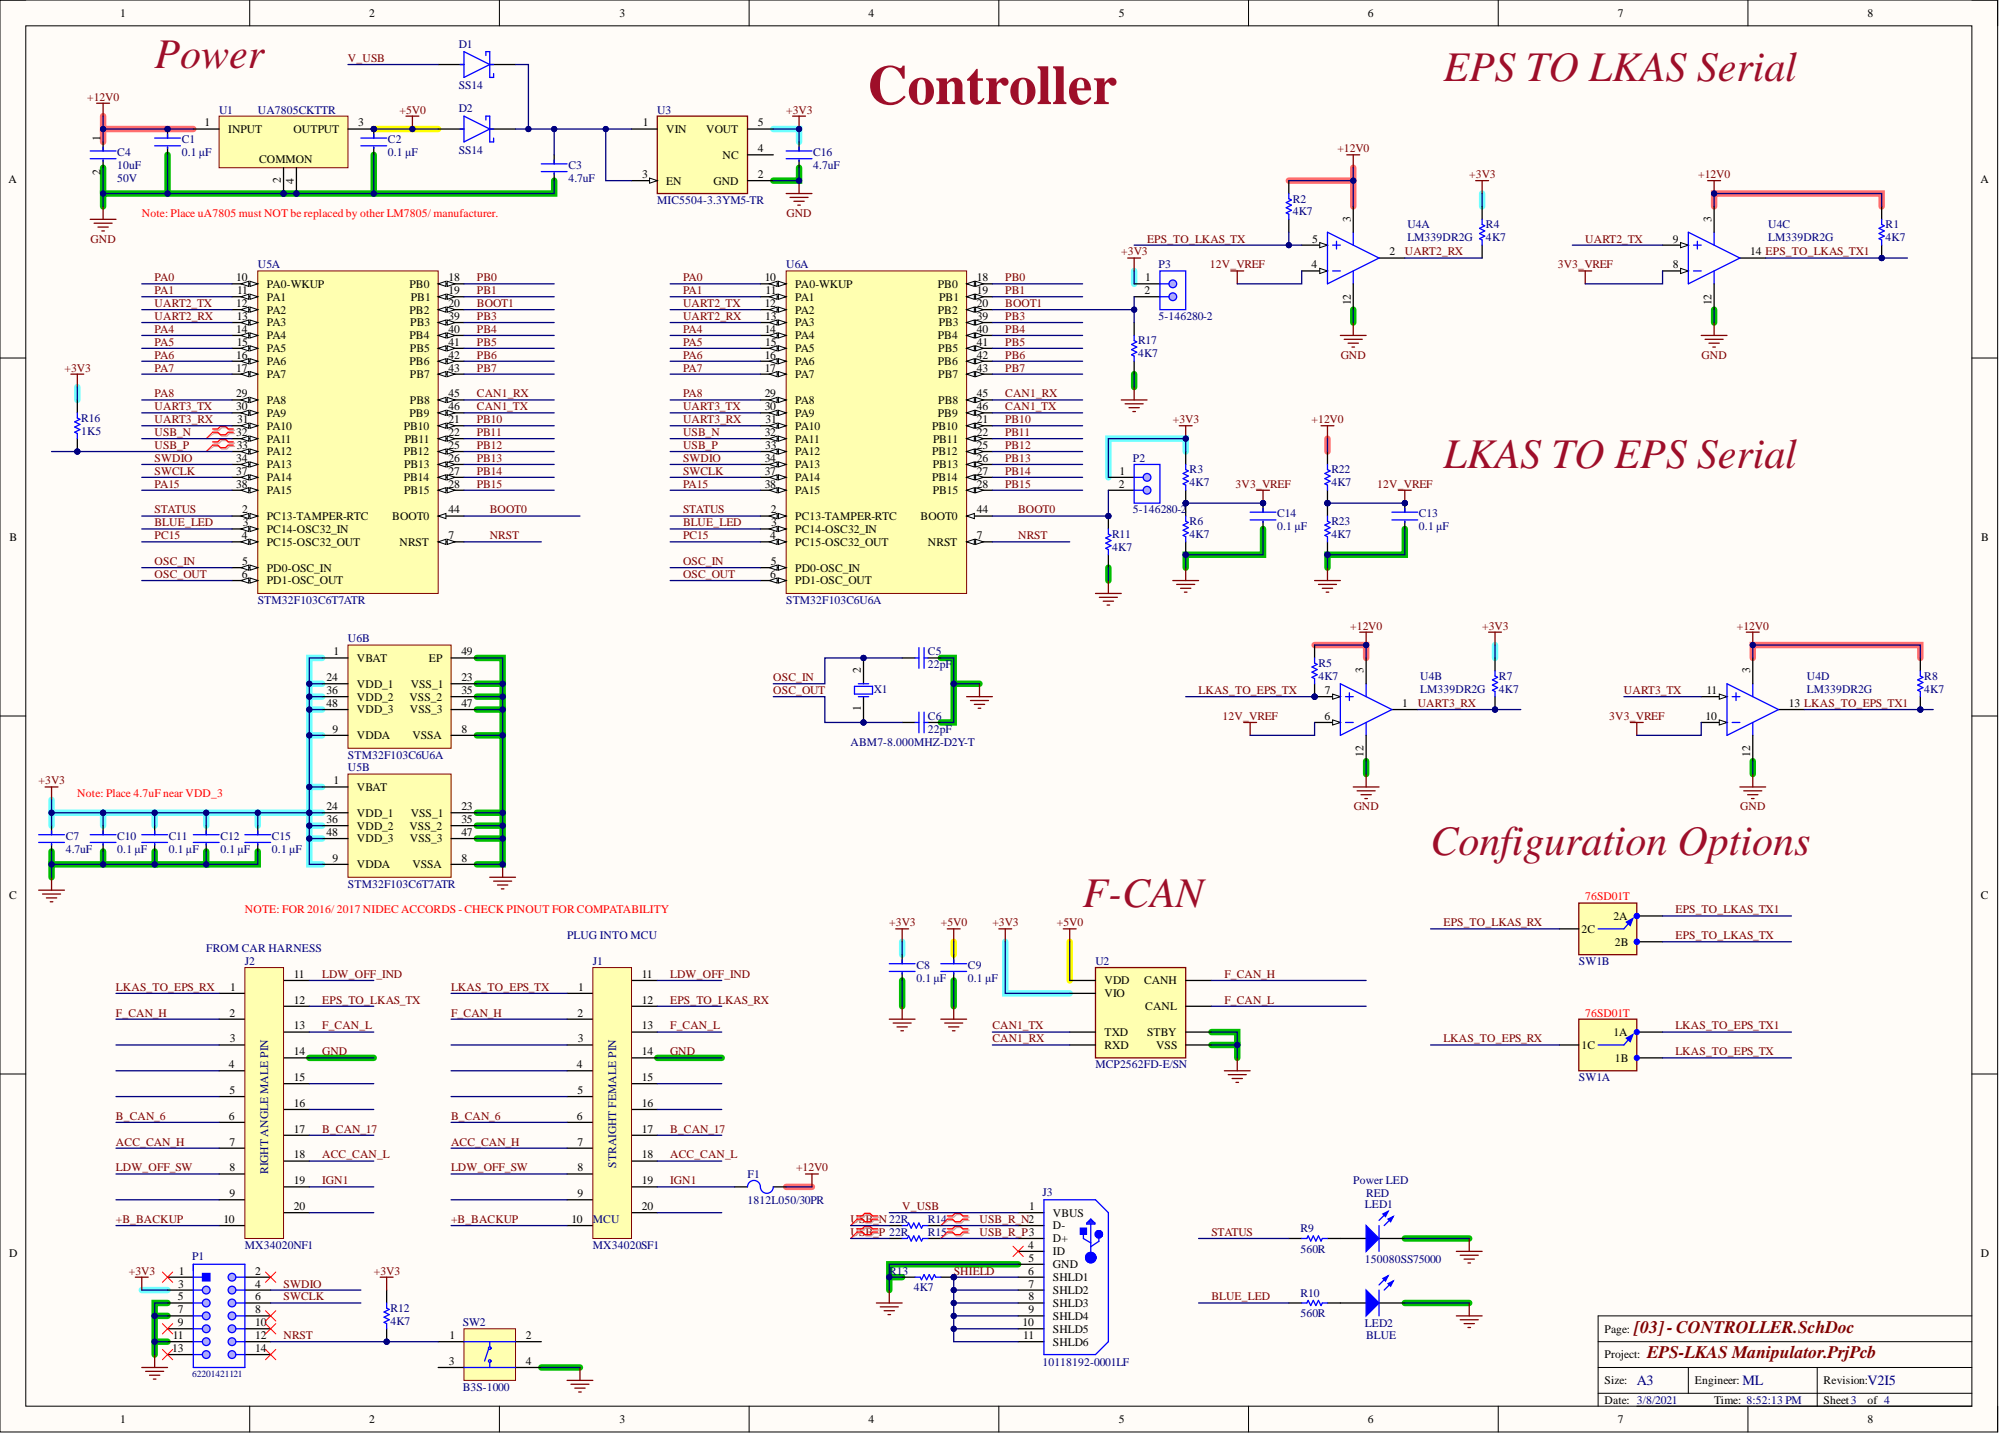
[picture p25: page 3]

EPS TO LKAS Serial

Note: Place uA7805 must NOT be replaced by other LM7805/ manufacturer.

LKAS TO EPS Serial

NOTE: FOR 2016/ 2017 NIDEC ACCORDS - CHECK PINOUT FOR COMPATABILITY

RIGHT ANGLE MALE PIN

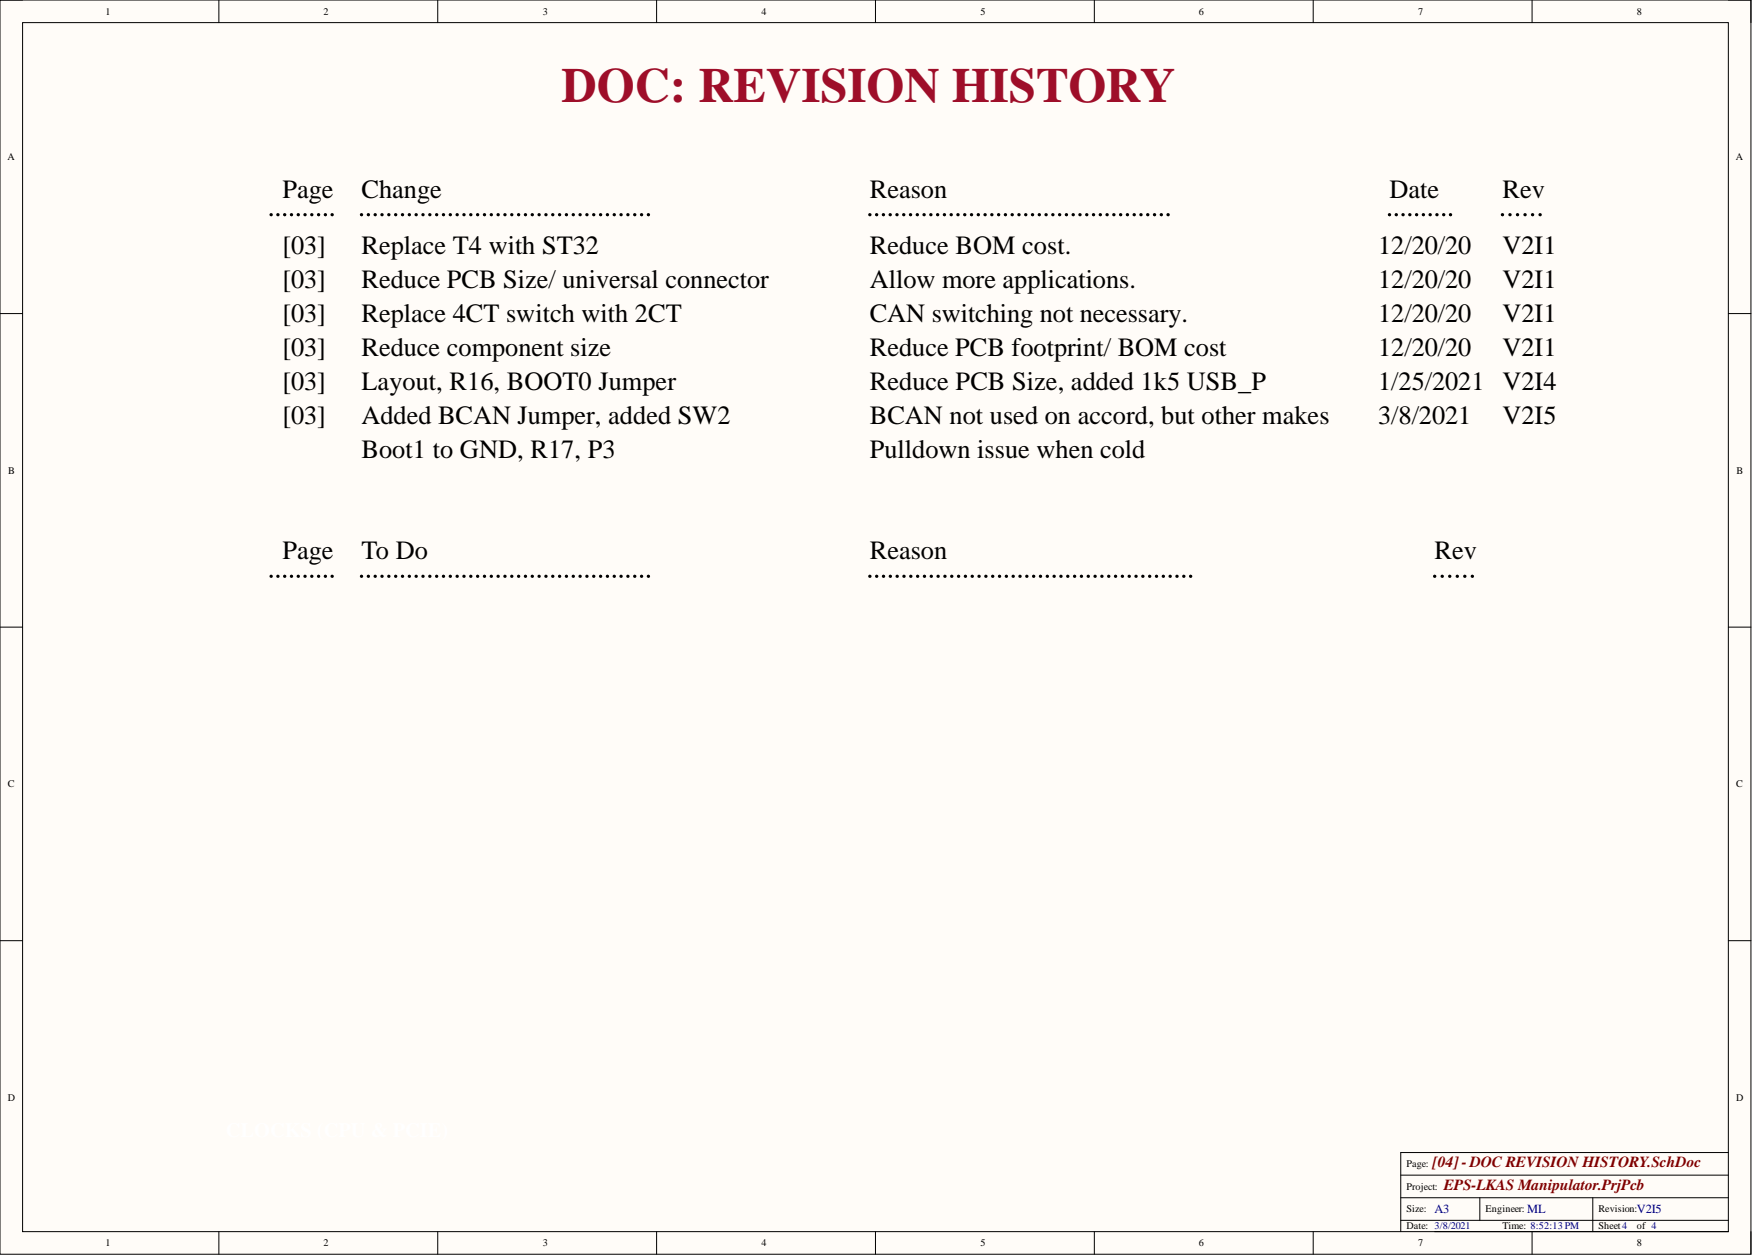
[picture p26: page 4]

[04] - DOC REVISION HISTORY.SchDoc

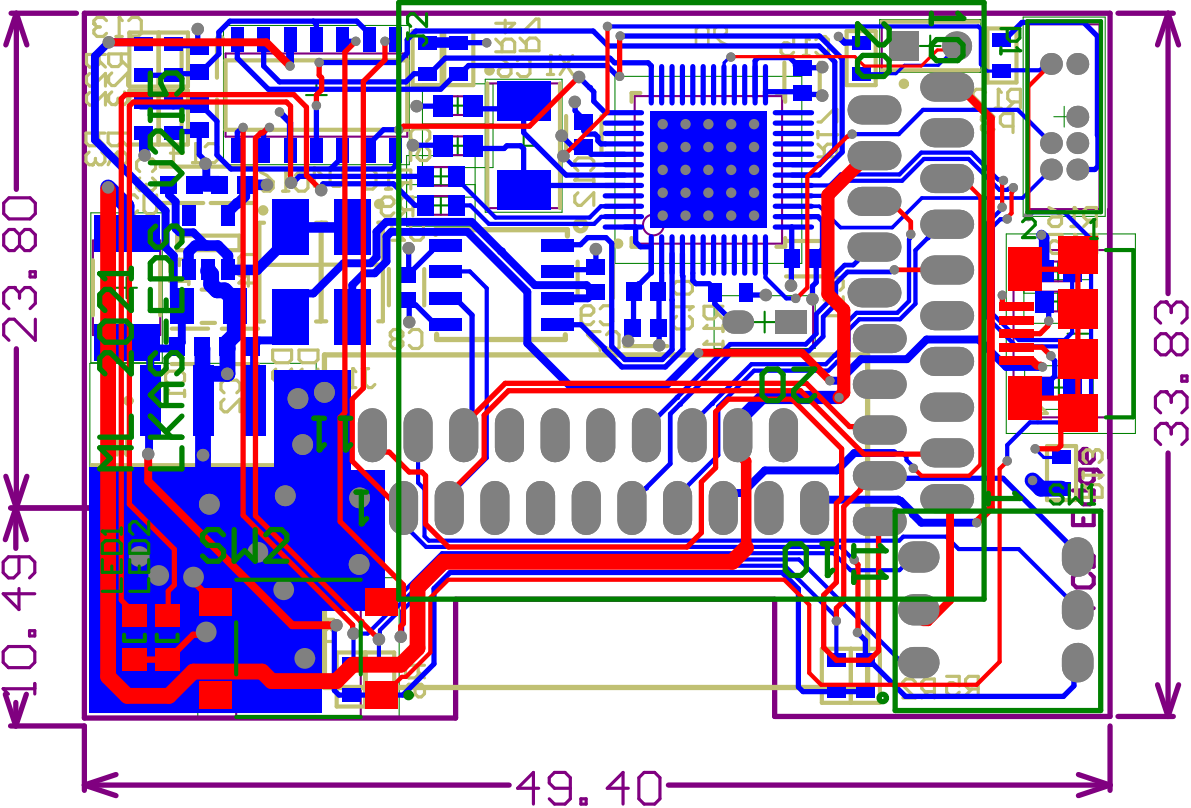
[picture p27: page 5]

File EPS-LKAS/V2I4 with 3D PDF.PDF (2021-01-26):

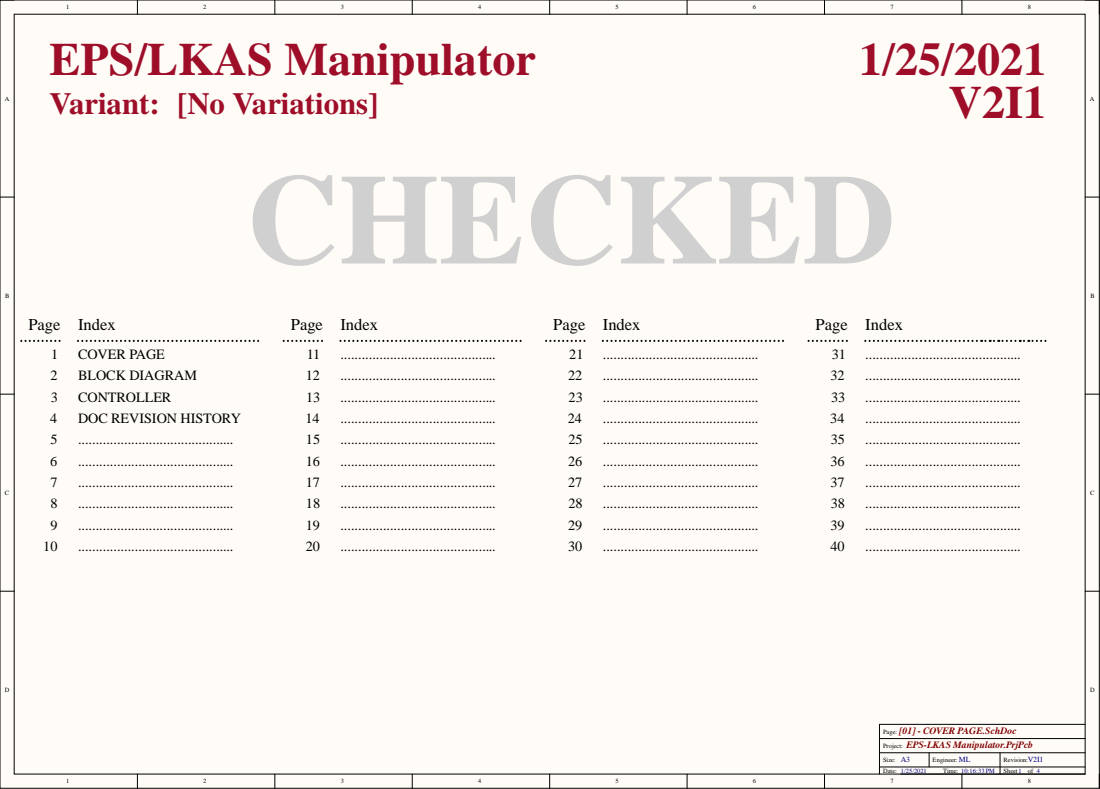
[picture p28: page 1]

[01] - COVER PAGE.SchDoc
Page:
Project: EPS-LKAS Manipulator.PrjPcb

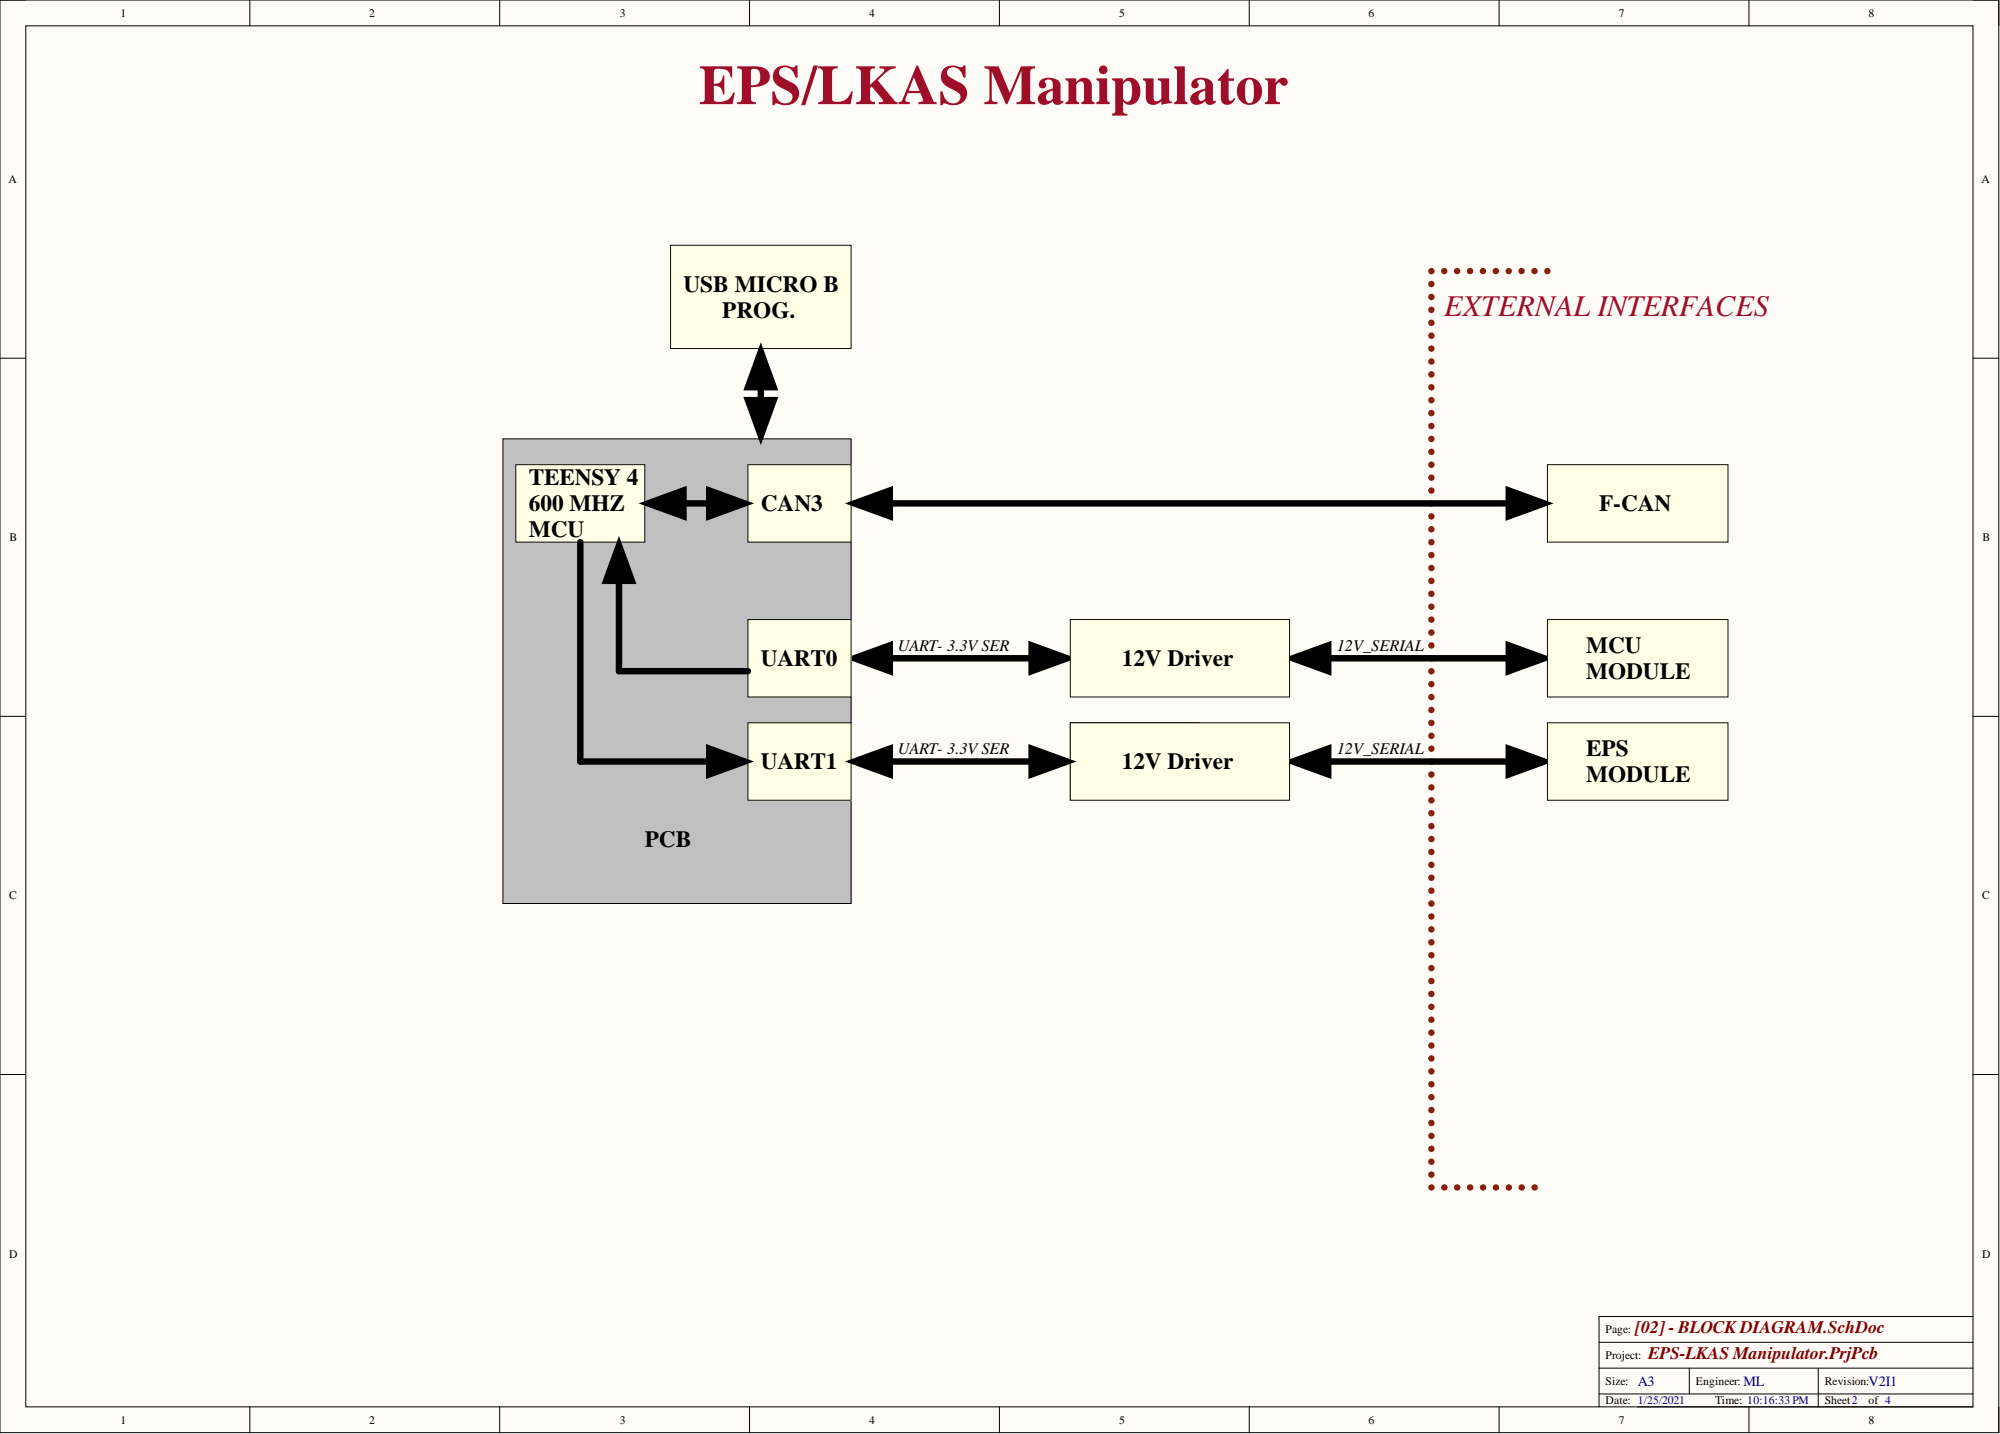
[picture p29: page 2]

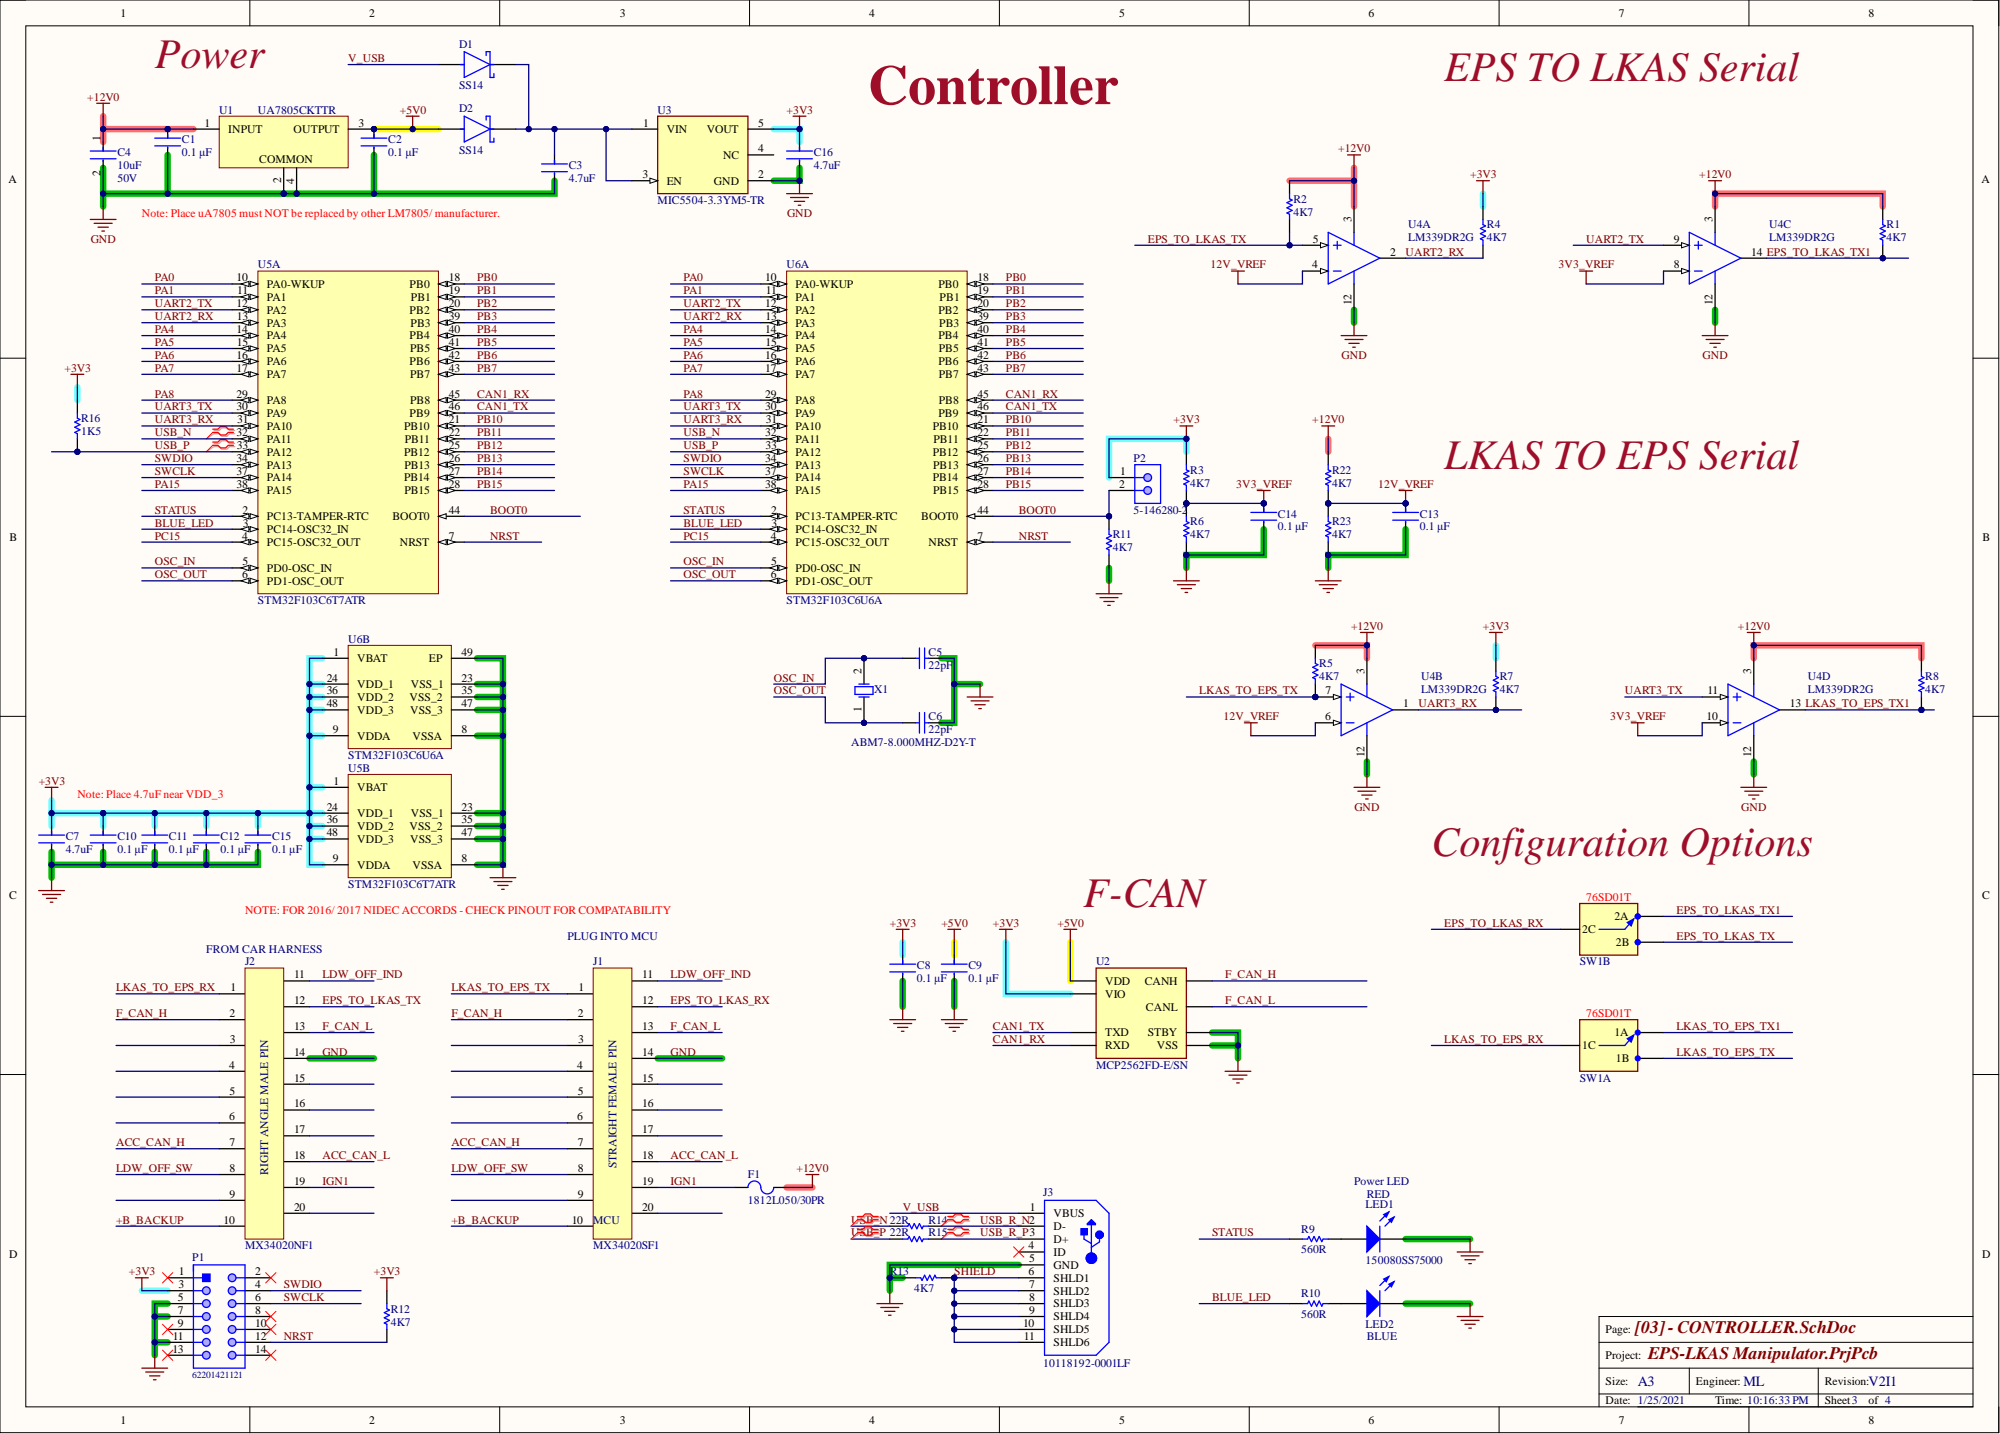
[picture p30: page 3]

EPS TO LKAS Serial

Note: Place uA7805 must NOT be replaced by other LM7805/ manufacturer.

LKAS TO EPS Serial

NOTE: FOR 2016/ 2017 NIDEC ACCORDS - CHECK PINOUT FOR COMPATABILITY

RIGHT ANGLE MALE PIN

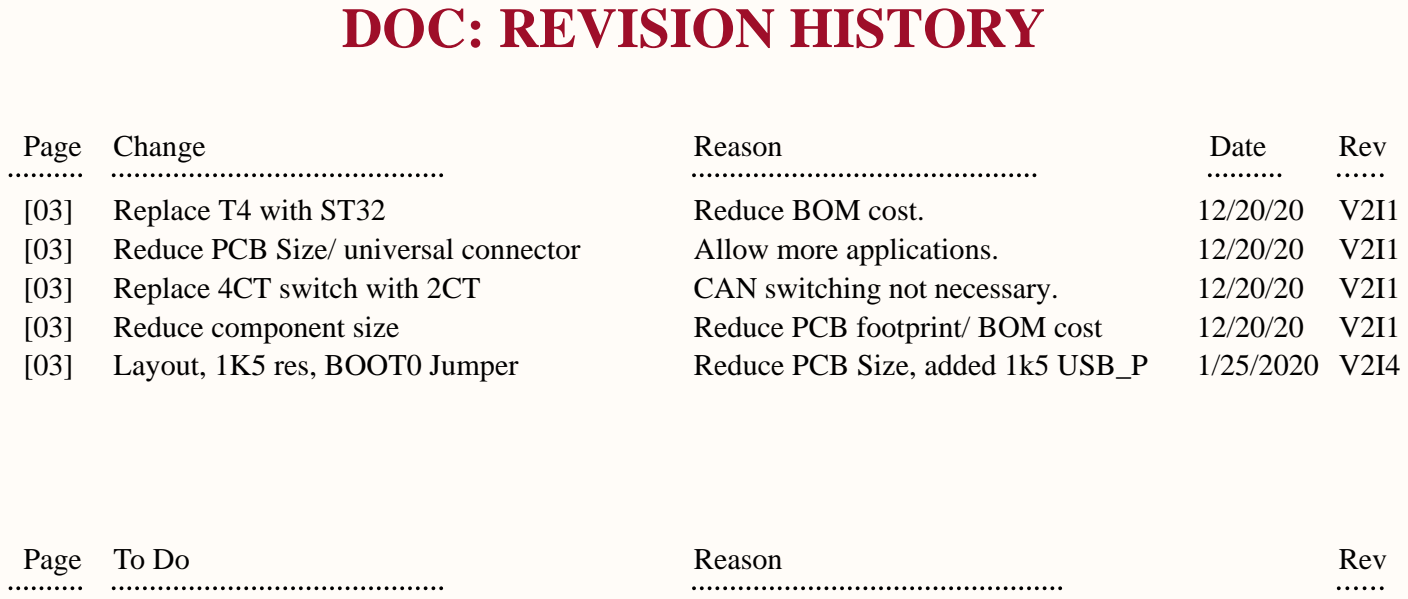
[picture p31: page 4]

[04] - DOC REVISION HISTORY.SchDoc

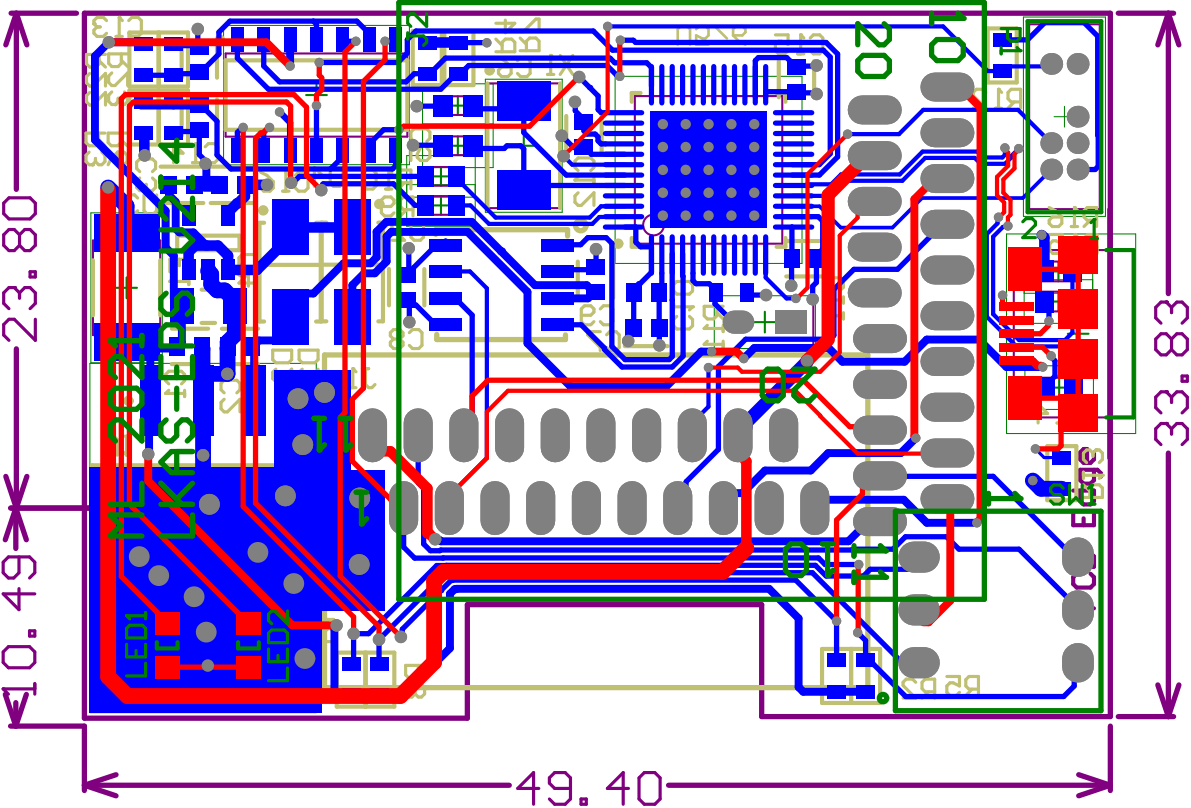
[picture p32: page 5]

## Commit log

2020-12-20 added BOM and removed unnecessary files
    [Bill of Materials-Debug IO Board.xlsx, Debug IO Board.PrjPcb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]
2020-12-21 removed bottom silkscreen
    [Bill of Materials-EPS-LKAS Manipulator.xlsx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]
2020-12-24 initial V2 commit, design in progress
    [Bill of Materials-EPS-LKAS Manipulator.xlsx, Bill of Materials-LKAS_EPS.xlsx, EPS-LKAS Manipulator.PrjPcb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]
2020-12-24 V2I2 regenerated output files, design in progress
    [Bill of Materials-EPS-LKAS Manipulator.xlsx, EPS-LKAS Manipulator.PrjPcb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]
2020-12-29 updated to use STM32F1 48 pin package. Added USB programming Port, added OR for 3.3V input
    [Bill of Materials-EPS-LKAS Manipulator.xlsx, Bill of Materials-LKAS_EPS.xlsx, EPS-LKAS Manipulator.PrjPcb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]
2021-01-07 Updated, cleaned files and regenerated gerber after last modification
    [Bill of Materials-EPS-LKAS Manipulator.xlsx, EPS-LKAS Manipulator.PrjPcb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]
2021-01-15 Updated to V2I4
    [Bill of Materials-EPS-LKAS Manipulator.xlsx, DO NOT USE LKAS-EPS_PCB_V2I1.PcbDoc, DO NOT USE LKAS-EPS_PCB_V2I3.PcbDoc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]
2021-01-19 Resized board to fit under cover, V2I4 layout
    [EPS-LKAS Manipulator.PrjPcb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]
2021-01-26 Added 1K5 USB_P
    [LKAS-EPS_PCB_V2I4.GBL, LKAS-EPS_PCB_V2I4.GBO, LKAS-EPS_PCB_V2I4.GBP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]
2021-03-09 Fixed various issues, updated V2I4 to V2I5, see PAGE 4 of sch for changes
    [Bill of Materials-EPS-LKAS Manipulator.xlsx, DO NOT USE LKAS-EPS_PCB_V2I1.PcbDoc, DO NOT USE LKAS-EPS_PCB_V2I3.PcbDoc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]
